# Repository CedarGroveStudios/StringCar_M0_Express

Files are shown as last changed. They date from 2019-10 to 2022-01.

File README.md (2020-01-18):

# StringCar_M0_Express

A Circuit-Python compatible string car racer controller board.

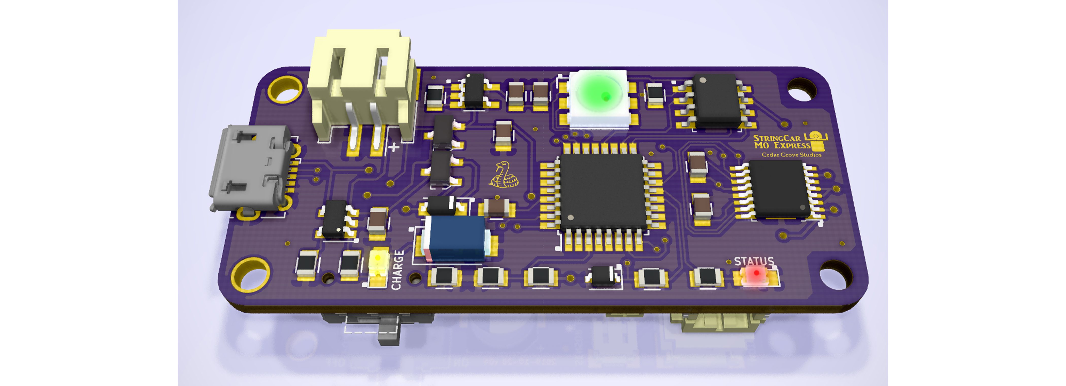
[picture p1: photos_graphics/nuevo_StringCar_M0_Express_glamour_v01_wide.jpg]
Glamour Shot


The Cedar Grove StringCar M0 Express is an ATSAMD21-based CircuitPython compatible board used to control a simple string car racer robot. The board is architecturally similar to the Adafruit Trinket M0 and ItsyBitsy M0 Express microcontroller boards with the addition of battery management and a DC motor controller. This board features JST connectors for the racer's battery, motor output, and sensor input. LiPo battery management charge rate is 500mA. For sensor experimentation, a 3.3-volt Stemma-QT connection is available on-board. The micro-USB connector is used for REPL operation, operational status data output, and battery charging. On-board flash memory size is 2MB.

The StringCar M0 Express board will not be sold. The GitHub repository will contain design files and links for the BOM and to the shared OSH Park project.

The string car racer is a simple one-motor robot that is suspended from a string using a pulley attached to the motor shaft. Its challenge is to race back and forth from one end of a taut string to the other. The fastest car wins. The controller board uses sensor switches to detect the ends of the string, calculate the string length, then control motor speed and braking to avoid string-end collisions.

The objective is to create a string car racer that can autonomously learn about its environment and adjust tradeoffs for speed and battery longevity. CircuitPython is used to easily add and interactively adjust performance features such as motor and battery efficiency, end-of-string collision avoidance, string length calculation, and predictive braking. Also, being able to watch its own battery status means that it'll always return to the home end of the string when battery capacity begins to wane. Circuit Python also supports libraries that abstract string car functions, simplifying the primary code module to make it easier for novice programmers to get involved in customizing  string car racer operation.

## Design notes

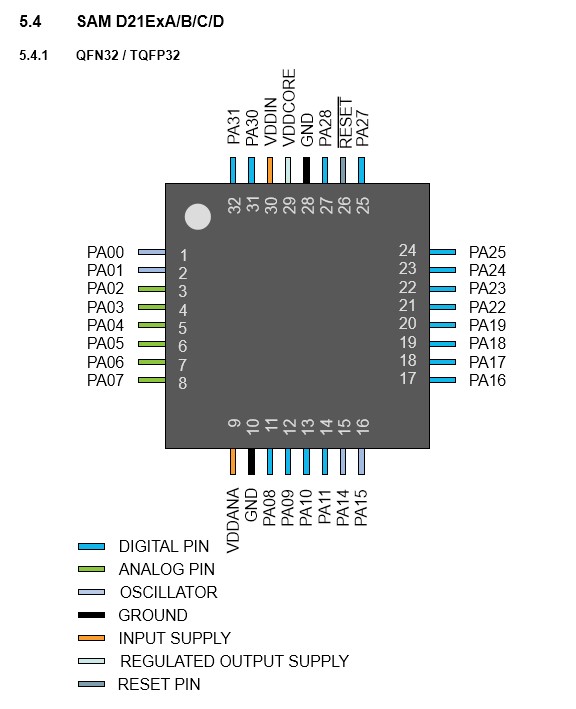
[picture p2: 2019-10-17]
design_references/samd21e pinout.jpg

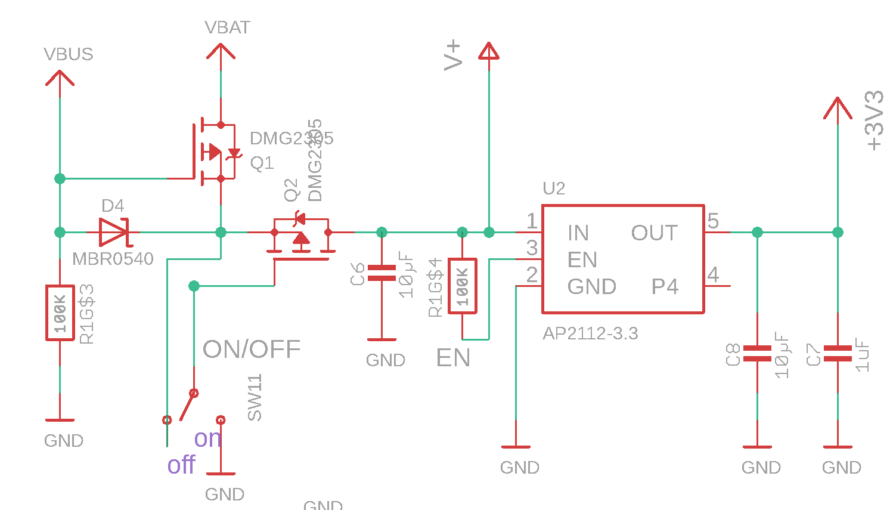
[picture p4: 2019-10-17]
design_references/PyGamer power mgt example.png

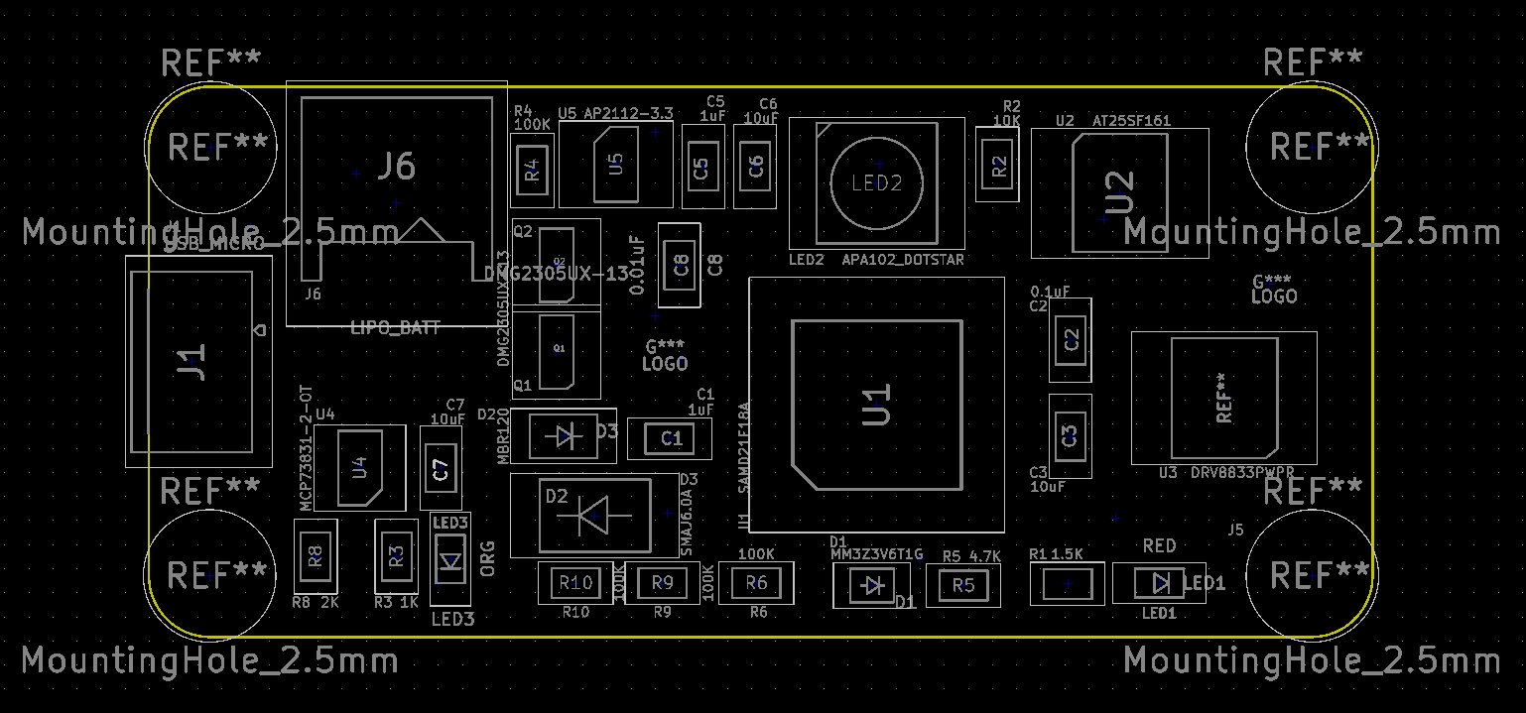
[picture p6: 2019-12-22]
photos_graphics/StringCar_M0_Express_PCB_layout.png

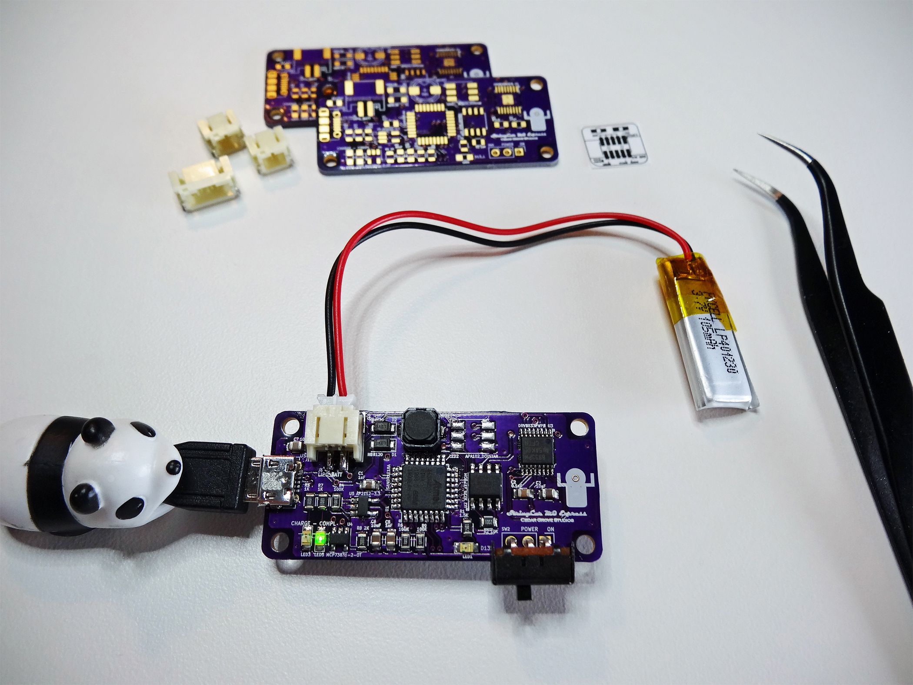
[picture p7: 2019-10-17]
photos_graphics/DSC05767a lores.jpg

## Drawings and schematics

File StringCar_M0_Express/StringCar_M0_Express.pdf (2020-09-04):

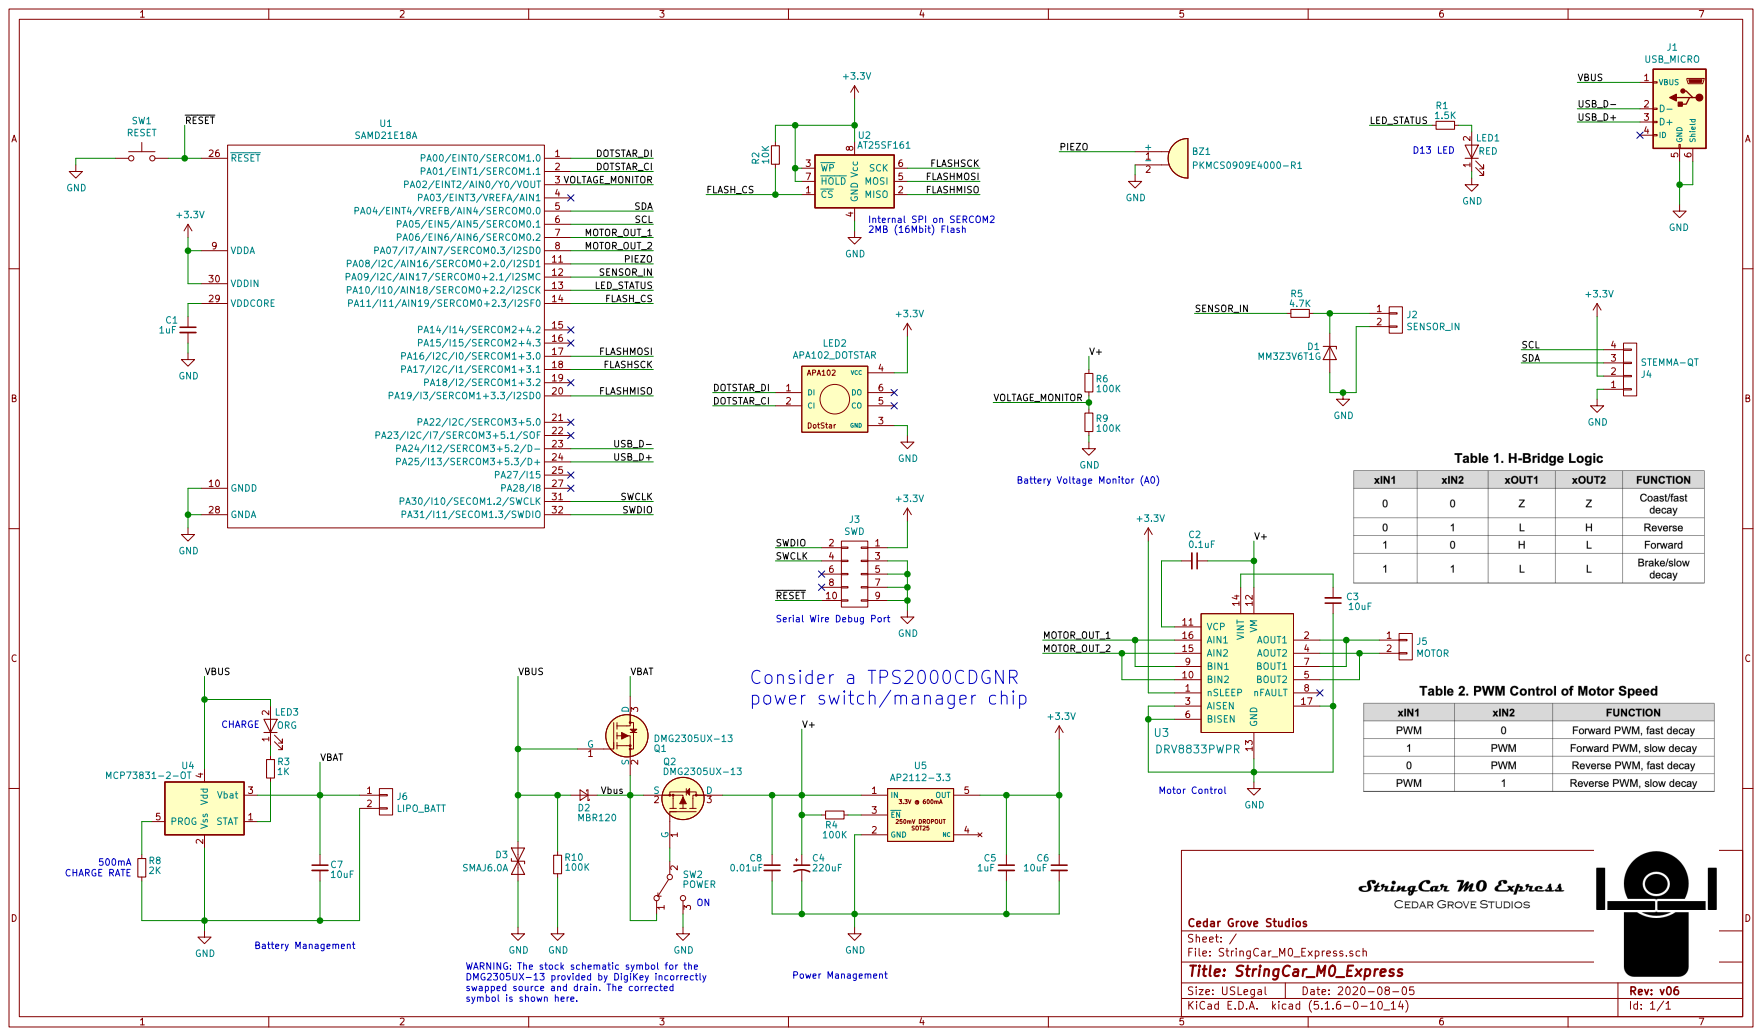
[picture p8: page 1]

4 MOSI 5 SCK 6 HOLD 7 Vcc 8 U2AT25SF161

Consider a TPS2000CDGNR
power switch/manager chip

D Date: 2020-08-05 KiCad E.D.A. kicad (5.1.6-0-10_14)
File: StringCar_M0_Express.sch Sheet: / Cedar Grove Studios

WARNING: The stock schematic symbol for the
DMG2305UX-13 provided by DigiKey incorrectly
swapped source and drain. The corrected
symbol is shown here.

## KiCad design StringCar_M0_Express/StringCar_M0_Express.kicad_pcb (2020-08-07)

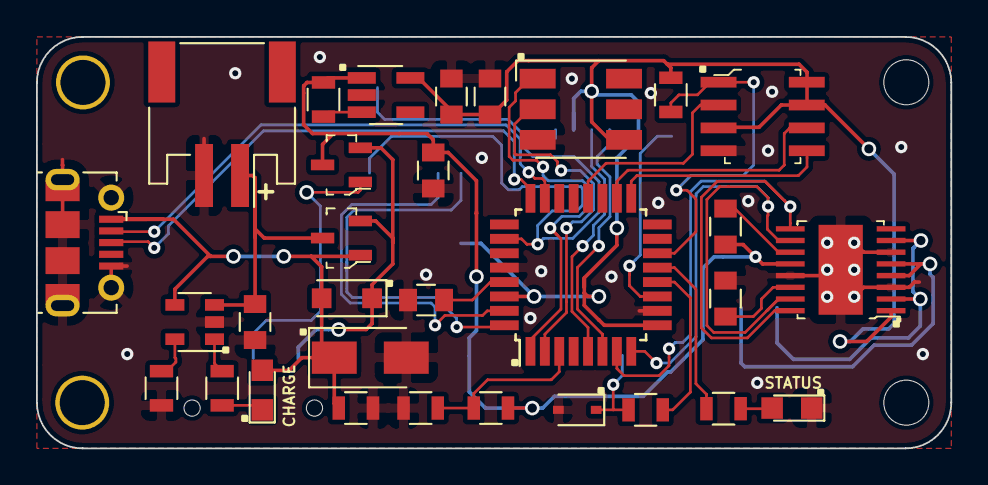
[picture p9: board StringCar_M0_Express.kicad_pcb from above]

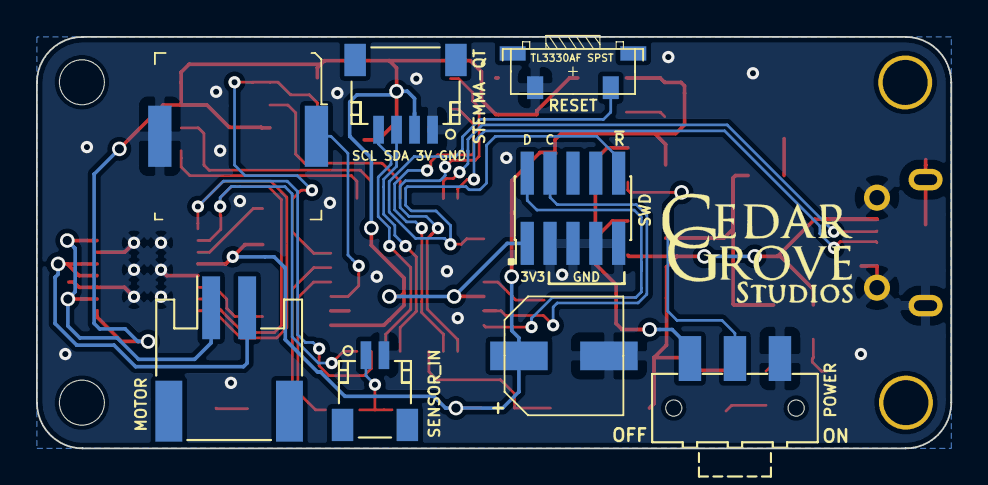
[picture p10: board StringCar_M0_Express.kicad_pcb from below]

Board: 2 copper layers, 50.8 x 22.9 mm, 39 parts (8 on the bottom side), 37 nets.

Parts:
BZ1: PKMCS0909E4000-R1; Piezo_9x9mm_PKMCS0909E4000-R1
C1, C5: 1uF; C_0805
C2: 0.1uF; C_0805
C3, C6, C7: 10uF; C_0805
C4: 220uF; CP_Elect_6.6x6.6
C8: 0.01uF; C_0805
D1: MM3Z3V6T1G; D_SOD-323
D2: MBR120; D_SOD-123F
D3: SMAJ6.0A; D_SMA
J1: USB_MICRO; USB_Micro-B_Molex-105017-0001
J2: SENSOR_IN; JST_SH_SM02B-SRSS-TB_02x1.00mm_Angled
J3: SWD; Pin_Header_Straight_2x05_Pitch1.27mm_SMD
J4: STEMMA-QT; JST_SH_SM04B-SRSS-TB_04x1.00mm_Angled
J5: MOTOR; JST_PH_S2B-PH-SM4-TB_02x2.00mm_Angled
J6: LIPO_BATT; JST_PH_S2B-PH-SM4-TB_02x2.00mm_Angled
LED1: RED; LED_0805
LED2: APA102_DOTSTAR; LED_RGB_5050-6
LED3: ORG; LED_0805
Q1, Q2: DMG2305UX-13; SOT-23-3
R1: 1.5K; R_0805
R2: 10K; R_0805
R3: 1K; R_0805
R4, R6, R9, R10: 100K; R_0805
R5: 4.7K; R_0805
R8: 2K; R_0805
SW1: RESET; TL3330AF_SPST_BUTTON_RT-ANGLE_7.8mm_2.5mm_2.5mm
SW2: POWER; SW_SPDT_CK-JS102011SAQN
U1: SAMD21E18A; TQFP-32_7x7mm_Pitch0.8mm
U2: AT25SF161; SOIC-8_W3.9mm
U3: DRV8833PWPR; TSSOP-16-1EP_W4.40mm
U4: MCP73831-2-OT; SOT-23-5
U5: AP2112-3.3; SOT-23-5_HandSoldering

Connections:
+3V3: C5.1, C6.1, J3.1, J4.2, LED2.4, R2.1, U1.9, U1.30, U2.3, U2.7, U2.8, U3.1, U5.5
/DOTSTAR_CI: LED2.2, U1.2
/DOTSTAR_DI: LED2.1, U1.1
/FLASHMISO: U1.20, U2.2
/FLASHMOSI: U1.17, U2.5
/FLASHSCK: U1.18, U2.6
/FLASH_CS: R2.2, U1.14, U2.1
/LED_STATUS: R1.2, U1.13
/MOTOR_OUT_1: U1.7, U3.9, U3.16
/MOTOR_OUT_2: U1.8, U3.10, U3.15
/PIEZO: BZ1.1, U1.11
/SCL: J4.4, U1.6
/SDA: J4.3, U1.5
/SENSOR_IN: R5.2, U1.12
/SWCLK: J3.4, U1.31
/SWDIO: J3.2, U1.32
/USB_D+: J1.3, U1.24
/USB_D-: J1.2, U1.23
/V+: C2.1, C4.1, C8.1, Q2.3, R4.2, R6.2, U3.12, U5.1
/VBAT: C7.1, J6.1, Q1.3, U4.3
/VBUS: D2.2, D3.1, J1.1, LED3.2, Q1.1, R10.2, U4.4
/VOLTAGE_MONITOR: R6.1, R9.2, U1.3
/Vbus: D2.1, Q1.2, Q2.2, SW2.1
/~RESET: J3.10, SW1.2, U1.26
GND: BZ1.2, C1.2, C3.1, C4.2, C5.2, C6.2, C7.2, C8.2, D1.2, D3.2, J1.5, J1.6, J2.2, J3.3, J3.5, J3.7, J3.9, J4.1, J6.2, LED1.1, LED2.3, R8.1, R9.1, R10.1, SW1.1, SW2.3, U1.10, U1.28, U2.4, U3.3, U3.6, U3.13, U3.17, U4.2, U5.2
unnamed: C1.1, U1.29
unnamed: C2.2, U3.11
unnamed: C3.2, U3.14
unnamed: D1.1, J2.1, R5.1
unnamed: J5.1, U3.2, U3.7
unnamed: J5.2, U3.4, U3.5
unnamed: LED1.2, R1.1
unnamed: LED3.1, R3.2
unnamed: Q2.1, SW2.2
unnamed: R3.1, U4.1
unnamed: R4.1, U5.3
unnamed: R8.2, U4.5

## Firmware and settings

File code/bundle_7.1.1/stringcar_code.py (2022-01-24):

# boomerpong gen_2 2021-03-05 v25.py
# experimental version for StringCar M0 Express
# library: stringcar 2021-03-05 v09.py
print("boomerpong gen_2 2021-03-05 v25.py")

import time
import stringcar as sc

#   ### MOTOR SPECIFICATIONS ###
# motor characteristics for BoomerPong gen_2 3v 2700RPM motor (RF-500TB-18280)
stop_motor_volt = 0.3
min_motor_volt = 0.6
max_motor_volt = 4.7
power_volt = 4.7  # battery monitoring could change this parameter
accel_rate = 0.5  # stop to max speed accel/decel (sec)
# rated_motor_volt = 5.0
# rated_motor_rpm = 2700
# effective_pulley_dia_inch = 0.16

motor_specs = stop_motor_volt, min_motor_volt, max_motor_volt, power_volt, accel_rate

#   ### VARIABLES ###
speed = 0       # -1.0 (rev) to +1.0 (fwd)
lap = -1
dist = 0        # (sec)

# ### SETTINGS and SETUP ####

# play hello tune
sc.hello()

# send motor specifications to stringcar library
# wait to start, then receive min speed, accel rate, and mode values
min_speed, mode, motor_params = sc.setup(motor_specs)
print(f"BATTERY VOLTAGE = {sc.get_batt():3.1f}v     : CPU TEMPERATURE = {sc.cpu_temp():3.1f}˚F")
print(f"MINIMUM SPEED   = {min_speed:3.3f}    : MODE = {mode}")
print(f"MOTOR VOLTS SPECIFICATIONS : stop = {motor_specs[0]:3.1f}v   min = {motor_specs[1]:3.1f}v")
print(f"                             max = {motor_specs[2]:3.1f}v    power_source = {motor_specs[3]:3.1f}v")
print(f"                             accel_rate = {motor_specs[4]:4.3f}")
print(f"MOTOR DUTY_CYCLE PARAMETERS: zero = {motor_params[0]:3.3f}  min = {motor_params[1]:3.3f}  max = {motor_params[2]:3.3f}")

sc.time.sleep(1)  # allow time to remove hand from car

# set initial direction to reverse; it'll get flipped later
direction = -1
sc.busy.value = False

# #### MAIN LOOP #####
while True:
    lap = lap + 1

    # Boomerang stop at end of lap 1
    if not mode and lap > 1:
        speed = sc.accel(speed, 0, 0, motor_params) # release the brakes
        print("end of Boomerang lap")
        while True:
            sc.beep_on(494)
            sc.flash(7, 1, .01, 3)
            sc.beep_off(.5)
            print(".")

    t0 = time.monotonic()
    dist = 0

    direction = direction * -1  # flip motor direction
    if lap == 0:
        speed = sc.accel(speed, min_speed * direction, accel_rate, motor_params)
        at_min_speed_flag = True
    else:
        speed = sc.accel(speed, 1.0 * direction, accel_rate, motor_params)
        at_min_speed_flag = False

    # escape EOS
    while not sc.sensor_eos.value:
        sc.busy.value = True
        dist = time.monotonic() - t0

        # 1+ laps and at slowing dist and at maximum speed
        if lap > 0 and dist > (str_len) and not at_min_speed_flag:
            at_min_speed_flag = True
            speed = sc.accel(speed, min_speed * direction, accel_rate, motor_params)
    sc.busy.value = False

    # normal travel; wait for EOS
    while sc.sensor_eos.value:
        dist = time.monotonic() - t0

        # 1+ laps and at slowing dist and at maximum speed
        if lap > 0 and dist > str_len and not at_min_speed_flag:
            at_min_speed_flag = True
            speed = sc.accel(speed, min_speed * direction, accel_rate, motor_params)

    # insert LOST test here
    speed = sc.speed(0, motor_params) # put on the brakes
    sc.busy.value = True
    sc.beep_on(656)  # E5
    sc.time.sleep(0.5)
    sc.beep_off()

    # string length calculation
    if lap == 0:
        # calibration lap; scale string length to max speed based on min speed
        #   dist-(accel_rate/2) is adjusted distance with initial accel to min speed
        str_len = (dist - (accel_rate / 2)) * min_speed
        print(f"CALIBRATE lap = {lap:3.0f} : dist = {dist:6.3f} :     str_len = {str_len:6.3f} : min speed = {min_speed:6.3f}")
    else:
        # calculate new string length
        if dist > str_len:
            # adjust distance if longer than previous string length
            #   str_len is initial distance including initial accel to max speed
            #   ((dist-str_len)*min_speed) is raw dist measured after str_len is reached
            #   ((accel_rate/2)*(1.0-min_speed)) is slowing distance from full to min speed
            dist = str_len + ((dist - str_len) * min_speed) + ((accel_rate / 2) * (1.0 - min_speed))

        # use moving average to approximate the new string length
        #   (also known as successive approximation)
        str_len = (str_len + ((dist - str_len)/2))
        print(f"      RUN lap = {lap:3.0f} : dist = {dist:6.3f} : NEW str_len = {str_len:6.3f}")

    # return to top of the main loop

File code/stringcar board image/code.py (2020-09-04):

# Cedar Grove StringCar M0 Express Demo
# Cedar Grove StringCar M0 Express Demo

import board
import time
import pulseio
from digitalio import DigitalInOut, Direction, Pull
from analogio import AnalogIn
import adafruit_dotstar as dotstar
from simpleio import map_range, tone

# Red Status LED
led = DigitalInOut(board.LED_STATUS)
led.direction = Direction.OUTPUT
led.value = False

# The RGB LED
dot = dotstar.DotStar(board.DOTSTAR_CI, board.DOTSTAR_DI, 1, brightness=0.1)
dot[0] = (128, 0, 128)  # yellow startup status

import busio

try:
    stemma = busio.I2C(board.SCL, board.SDA)
    stemma_connected = True
    print("STEMMA DEVICE CONNECTED")
except:
    stemma_connected = False
    print("Stemma device disconnected")
    time.sleep(3)

# Analog input on VOLTAGE_MONITOR
v_plus = AnalogIn(board.VOLTAGE_MONITOR)

# Motor controller outputs
motor_out_1 = DigitalInOut(board.MOTOR_OUT_1)
motor_out_1.direction = Direction.OUTPUT
motor_out_2 = DigitalInOut(board.MOTOR_OUT_2)
motor_out_2.direction = Direction.OUTPUT

# Piezo speaker outputs
piezo = board.PIEZO
tone(piezo, 880, duration=0.3)  # A5

# Sensor input with pullup on SENSOR_IN
sensor = DigitalInOut(board.SENSOR_IN)
sensor.direction = Direction.INPUT
sensor.pull = Pull.UP


######################### HELPERS ##############################

# Helper to convert analog input to voltage
def getVoltage(pin):
    return 2 * (pin.value * 3.3) / 65536

# Helper to give us a nice color swirl
def wheel(pos):
    # Input a value 0 to 255 to get a color value.
    # The colours are a transition r - g - b - back to r.
    if (pos < 0) or (pos > 255):
        return (0, 0, 0)
    if pos < 85:
        return (int(255 - pos*3), int(pos*3), 0)
    elif pos < 170:
        pos -= 85
        return (0, int(255 - (pos*3)), int(pos*3))
    else:
        pos -= 170
        return (int(pos*3), 0, int(255 - pos*3))

######################### MAIN LOOP ##############################


i = 0
while True:
  led.value = True
  motor_out_1.value = True
  motor_out_2.value = False

  # spin internal LED around! autoshow is on
  dot[0] = wheel(i & 255)

  if sensor.value: sens = 3.3
  else: sens = 0

  # Read analog voltage on VOLTAGE_MONITOR
  print((i & 255))
  print('i: %3.0f  wheel: %6x' % (i, i & 255), wheel(i & 255))
  print("V+ : %0.2f" % (2 * getVoltage(v_plus)))
  print( (getVoltage(v_plus), sens))

  if not sensor.value:
      print("Sensor closed to ground!")

  i = (i+1) % 256  # run from 0 to 255

  led.value = False
  motor_out_1.value = False
  motor_out_2.value = True

  time.sleep(0.05) # make bigger to slow down

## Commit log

2019-10-17 initial repo load
    [StringCar CPy PCB-B.Cu.gbl, StringCar CPy PCB-B.Mask.gbs, StringCar CPy PCB-B.SilkS.gbo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]
2019-10-21 update pcb layout and logo graphics
    [StringCar CPy PCB-B.Cu.gbl, StringCar CPy PCB-B.Mask.gbs, StringCar CPy PCB-B.SilkS.gbo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]
2019-10-21 update board layout and graphics
2019-11-17 update footprints
    [StringCar_M0_Express.sch]
2019-12-22 update board layout graphic
    [StringCar_M0_Express.kicad_pcb]
2020-01-18 repair schematic and regenerate PCB as v05
    [StringCar_M0_Express-B.Cu.gbl, StringCar_M0_Express-B.Mask.gbs, StringCar_M0_Express-B.SilkS.gbo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]
2020-01-18 fix schematic and update PCB to v05
    [StringCar_M0_Express-B.Cu.gbl, StringCar_M0_Express-B.Mask.gbs, StringCar_M0_Express-B.SilkS.gbo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]
2020-01-18 update schematic with symbol correction; add warning
    [StringCar_M0_Express.sch]
2020-07-31 correct stemma-qt pinout
    [StringCar_M0_Express-B.Cu.gbl, StringCar_M0_Express-B.Mask.gbs, StringCar_M0_Express-B.SilkS.gbo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]
2020-08-07 update PCB
    [StringCar_M0_Express-B_Cu.gbl, StringCar_M0_Express-B_Mask.gbs, StringCar_M0_Express-B_Paste.gbp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]
2020-09-01 update schematic
    [StringCar_M0_Express.sch]
2020-09-04 Update schematic and test code
    [StringCar_M0_Express.sch]
2020-09-07 update motor PWM frequency in library
2020-12-14 update to an improved PWM frequency
2021-03-06 update motor specs; change driver to braking mode
2021-04-13 update PCB solder paste clearance
2022-01-24 update for CircuitPython v7.1.1
